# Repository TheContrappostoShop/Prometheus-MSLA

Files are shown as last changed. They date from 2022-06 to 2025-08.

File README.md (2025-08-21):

<div align="center">
  <h1>Prometheus-MSLA (LEGACY)</h1>
</div>

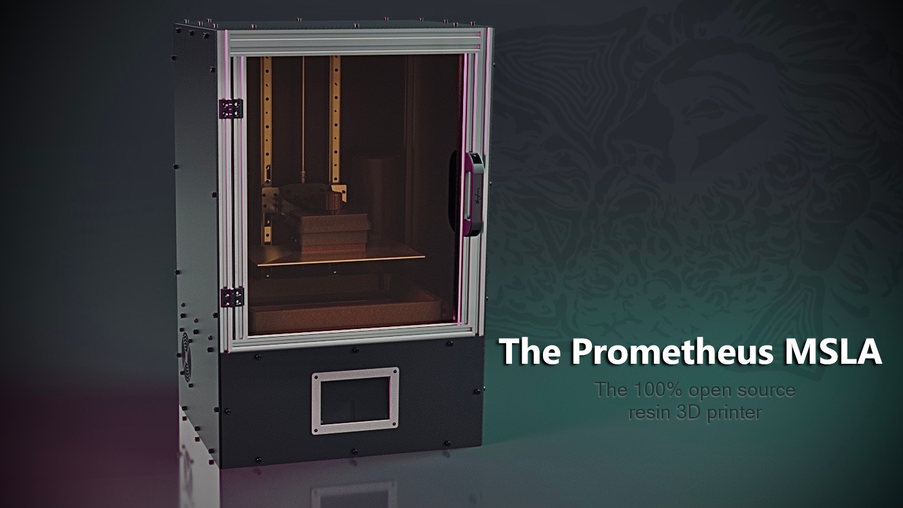
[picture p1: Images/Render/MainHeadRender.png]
Prometheus MSLA Printer Render! Open Source MSLA Printer Prometheus MSLA

Discord Link (https://discord.gg/6pFDJ3GbKh)

*DISCLAIMER ! THIS VERSION OF THE PROMETHEUS IS NOW NOT SUPPORTED DUE TO UNRELIABLE KEY COMPONENTS OF THE MACHINE SUCH AS THE LCD DUE TO DEFFECTIVE BATCHES FROM CHINESE MANUFACTURER. INSTEAD OF PATCHING THESE ISSUES, A NEW GENERATION OF PRINTER WILL BE CREATED.

The First fully open source MSLA 3D printer. The Prometheus MSLA is a large format printer with build volume of 298mm x 164mm x 350mm with a 13.7inch 7K monochrome display ( one of the largest and high resolution on the market ).

In greek mythology there is a legend of a Titan named Prometheus, he is known
for defying the gods by stealing fire and gifting it back to humanity.

Not only did he give them fire, Prometheus also taught humans how to use fire,
thus giving them the skill of metalwork, then ensued science and the arts,
allowing us to create everything we have today.

We created this project because we wanted to offer a machine that was accessible
to everyone, we wanted it to be easily modified so that you can create and give
your machine your own personal touch.

## Source and Documentation

### CAD
The full Prometheus Assembly can be viewed or downloaded over on
[GrabCAD](https://grabcad.com/library/the-prometheus-msla-v1-full-assembly-1)!

See [here](STL) for exported STLs of all of the printed parts, and
[here](Drawings) for the exported DXF files for the enclosure and base plates.

### Control Board
Prometheus Apollo Board EDA & Production Files Coming Soon!

### Firmware
For a fully configured Raspberry Pi image, check out
[PrometheusOS](https://github.com/TheContrappostoShop/PrometheusOS)!

You can also find our configuration files
[here](https://github.com/TheContrappostoShop/Prometheus_Config) for a manual
software install.

### Documentation
Finalized Build Guide Coming Soon!

In the mean-time, check out our
[Youtube Assembly Guide](https://www.youtube.com/watch?v=eP9PegG7pnA&list=PL1cx7A6ZVoZlWrnPsP4_g7WrTk8wNiGpT),
or join our Discord for advice and assistance!

## Community
If you want to share your experience or need more information, we are happy to
welcome you to our [Discord Server](https://discord.gg/GFUn9gwRsj).

## Licensing

License Statement CC BY-NC 4.0 (https://creativecommons.org/licenses/by-nc/4.0/)

This work is licensed under a <a rel="license" href="http://creativecommons.org/licenses/by-nc/4.0/">Creative Commons Attribution-NonCommercial 4.0 International License</a>.

## The Prometheus MSLA Team
|||
|-----|---|
| The Contrapposto Shop | Samuel (sam.boutin) and Melissa |
| CAD Modelling | Gil (rattus) and Shyam (eThing) |
| Electronics and Software | Paul (Paul_GD) and Ada (ragwafire) |
| The Rest of the Prometheus MSLA Team | Kristine (Elantris), Tyler, Stefan (Stuff!), Zakary, Zachary, Alain (Thewood3D) |

And thanks to all of those who helped, in one way or an other, on this open
source project!!

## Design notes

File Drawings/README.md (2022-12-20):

# Prometheus MSLA Panel & Plate Drawings
Here you can find all of the .dxf files for the enclosure panels and base/mid
plates for the Prometheus MSLA Printer.

## Enclosure Panels
All of the enclosure panels can be cut from 4mm (5/32") acrylic or ABS sheet.
The door panel should be transparent, if you wish to see inside the machine, but
beyond that basically any material may be used. Keep in mind, thicker or thinner
panels may require differently sized screws.

## Middle Plate and Base Plate
The "Middle Plate" and the "Base Plate" need to be about 12.5mm (1/2") thick.

You can use something like HDPE for easier cleaning, or even just MDF (which you
will need to seal) for a cheaper build.

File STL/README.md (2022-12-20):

# Prometheus MSLA Printed Parts STLs
Here you can find the .stl files for all of the 3D-printed parts for the
Prometheus MSLA Printer.

## Material
We recommend printing the vat in PLA or PETG! Other materials may react with the
chemicals in the resin.

The Structural parts (such as the arm) need to be very 
rigid--they can be printed in PLA, carbon fiber filled material, or other stiff
plastics.

## Print Settings
All the parts should be printed at 0.2mm layer height, with at least 35% infill
and at least 6 walls (with a .4 nozzle).

## Updates
For the latest versions of each part, see the full assembly [here](../CAD/).

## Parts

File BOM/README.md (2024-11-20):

# Bill Of Materials
> Note: Some listings on this page are affiliate links, to help support the project

| Category  | Description | Quantity  | Link  |
|---|---|---|---|
| *_Fasteners_* | | | |
| | M3 T-Nut | 18  | [Aliexpress](https://s.click.aliexpress.com/e/_DBXx7kr), [Amazon](https://amzn.to/3jPTPxT) |
| | M5 T-Nut | 137 | [Aliexpress](https://s.click.aliexpress.com/e/_DBXx7kr), [Amazon](https://amzn.to/3voWRi8) |
| | M3 Insert (L6mm)  | 46  | [Aliexpress](https://s.click.aliexpress.com/e/_DcgRRhD), [Amazon](https://amzn.to/381tYR5), [McMaster-Carr](https://www.mcmaster.com/94459A140/) |
| | M4 Insert (L6mm)  | 5 | [Aliexpress](https://s.click.aliexpress.com/e/_DcgRRhD), [Amazon](https://amzn.to/3vuExnA), [McMaster-Carr](https://www.mcmaster.com/94459A150/) |
| | M3x8 SHC | 38  | [Aliexpress](https://s.click.aliexpress.com/e/_DlgyRsJ), [McMaster-Carr](https://www.mcmaster.com/91290A113/) |
| | M3x10 SHC | 18 | [Aliexpress](https://s.click.aliexpress.com/e/_DlgyRsJ), [McMaster-Carr](https://www.mcmaster.com/91290A115/) |
| | M3x18 SHC | 8  | [Aliexpress](https://s.click.aliexpress.com/e/_DlgyRsJ), [McMaster-Carr](https://www.mcmaster.com/91290A121/) |
| | M3x20 Countersunk  | 4  | [Aliexpress](https://s.click.aliexpress.com/e/_Deg3Y3h)  |
| | M3x25 SHC | 14  | [Aliexpress](https://s.click.aliexpress.com/e/_DlgyRsJ) |
| | M3x10 Countersunk | 44  | [Aliexpress](https://s.click.aliexpress.com/e/_Deg3Y3h),[McMaster-Carr](https://www.mcmaster.com/91294A130/) |
| | M4x10 SHC | 13  | [Aliexpress](https://s.click.aliexpress.com/e/_DlgyRsJ),[McMaster-Carr](https://www.mcmaster.com/91290A144/) |
| | M5x8 SHC | 135 | [Aliexpress](https://s.click.aliexpress.com/e/_DlgyRsJ), [McMaster-Carr](https://www.mcmaster.com/91290A222/) |
| | M5x16 SHC | 22  | [Aliexpress](https://s.click.aliexpress.com/e/_DlgyRsJ), [McMaster-Carr](https://www.mcmaster.com/91290A232/) |
| | M8x50 rod (or set screw)| 1 | [Aliexpress](https://s.click.aliexpress.com/e/_Dd8sriF), [McMaster-Carr](https://www.mcmaster.com/92015A151/) |
| | M3 Nut | 6 | [Aliexpress](https://s.click.aliexpress.com/e/_DdFF1gf), [Amazon](https://amzn.to/3PisOlx), [McMaster-Carr](https://www.mcmaster.com/90592A085/) |
| | M4 Nut | 12  | [Aliexpress](https://s.click.aliexpress.com/e/_DdFF1gf), [Amazon](https://amzn.to/3FApYUP), [McMaster-Carr](https://www.mcmaster.com/90592A090/) |
| | M3 Washer | 8  | [Aliexpress](https://s.click.aliexpress.com/e/_DDZk2np), [Amazon](https://amzn.to/3FePfU3), [McMaster-Carr](https://www.mcmaster.com/93475A210/) |
| | M4 Washer | 4 | [Aliexpress](https://s.click.aliexpress.com/e/_DDZk2np), [Amazon](https://amzn.to/3HwZ4iS), [McMaster-Carr](https://www.mcmaster.com/93475A230/) |
| | M5 Washer | 13  | [Aliexpress](https://s.click.aliexpress.com/e/_DDZk2np), [Amazon](https://amzn.to/3h75RW4), [McMaster-Carr](https://www.mcmaster.com/93475A240/) |
| \*Ball Screw build | M4x16 SHC | 4 | [Aliexpress](https://s.click.aliexpress.com/e/_DlgyRsJ), [McMaster-Carr](https://www.mcmaster.com/91290A154/) |
| \*Ball Screw build | M5x35 SHC | 4 | [Aliexpress](https://s.click.aliexpress.com/e/_DlgyRsJ), [McMaster-Carr](https://www.mcmaster.com/91290A256/) |
| \*Blind Joint | M5 OR M6x12 BHC | 32  |  [Aliexpress](https://s.click.aliexpress.com/e/_DkBwHbz)  |
|||||
| *_Motion_* |
| | Nema 17 *0.9deg* (Bigger is better)| 1 | [Aliexpress](https://s.click.aliexpress.com/e/_Dl8Sp3z), [Amazon](https://amzn.to/3JTS9Ok) | [Spool3D](https://spool3d.ca/nema17-0-9-degree-stepper-motor-60mm/)
| | Linear Rails MGN12H 450mm | 2 | [Aliexpress](https://s.click.aliexpress.com/e/_DEJSeVN), [Amazon](https://amzn.to/3PisOlx),[Amazon](https://amzn.to/3uSQrbX)|
| | Coupling 5mm to 8mm | 1 | [Amazon](https://amzn.to/3xAs1Wk)|
| | Bearing | 1 | [Amazon](https://amzn.to/37tBqo3)|
| \*ACME build | ACME T8 2mm lead 500mm | 1 | [Aliexpress](https://s.click.aliexpress.com/e/_DDD1Mdz), [Amazon](https://amzn.to/3NEDFog) |
| \*ACME build | ACME Nut 2mm lead | 1 | [Spool3D](https://spool3d.ca/t8-lead-screw-anti-backlash-nut/) |
| \*Ball Screw Build 500 *ask Ali seller for coupler | Ball Screw 500mm 1204 | 1 | [Aliexpress](https://s.click.aliexpress.com/e/_DCBP8oT), [Amazon](https://amzn.to/41ezOoz)|
||||
| *_Electronics_* |
|*READ NOTES!* | LCD 7K 13.6inch | 1 | [Aliexpress](https://s.click.aliexpress.com/e/_Dex3wQn)|
|*READ NOTES!* | LCD HDMI Driver | 1 | [Aliexpress](https://s.click.aliexpress.com/e/_DeM0m83)|
|*READ NOTES!* | LCD + HDMI Driver *ALTERNATIVE* (Ask seller for driver) | 1 | [Alibaba](https://www.alibaba.com/product-detail/13-6-inch-7K-6480-3600_1600919542980.html)|
| | Inductive Probe 5v M12 NPN| 1 | [Aliexpress](https://s.click.aliexpress.com/e/_DcAIFCR), [Amazon](https://amzn.to/380BJGW)|
| | Power Supply 24v | 1 | [Aliexpress](https://s.click.aliexpress.com/e/_DdjQPYR), [Amazon](https://amzn.to/3EsALiw)|
| | IEC Socket | 1 | [Aliexpress](https://s.click.aliexpress.com/e/_DdLPQwn), [Amazon](https://amzn.to/3JSTPb1)|
| | 92mm 12v Fan | 2 | [Amazon](https://amzn.to/3rDMfL1)|
| | DSI Touch Screen | 1 | [Aliexpress](), [Amazon](https://amzn.to/3M15Rjr)|
| | DSI Flex Cable | 1 | [Amazon](https://amzn.to/3xArXWf)|
| | Raspberry pi 4B | 1 | [RPi Locator](https://rpilocator.com/?cat=PI4)|
| | Prometheus Control Board  | 1 | [Contrapposto Shop](https://www.contrapposto.shop)|
| | LED Array | 1 | [Aliexpress](https://s.click.aliexpress.com/e/_DmQAAPt)|
| | LED COB Fresnel (Alternative) | 1 | [Aliexpress](https://www.aliexpress.com/w/wholesale-sumaopai.html?spm=a2g0o.productlist.search.0)|
|||||
| *_Frame_* |
| | COMPLETE FRAME KIT (Blind joint)| 1  | [DLLPDF](https://www.dllpdf.com/prometheus-msla-structural-kit) |
| | 2020 Aluminum Extrusion - 490mm | 2  | [Aliexpress](https://s.click.aliexpress.com/e/_DCueqH9), [Amazon](https://amzn.to/3xlxGzp) |
| | 2020 Aluminum Extrusion - 450mm | 2  | [Aliexpress](https://s.click.aliexpress.com/e/_DCueqH9), [Amazon](https://amzn.to/3xhM6Ax) |
| | 2020 Aluminum Extrusion - 412mm | 6  | [Aliexpress](https://s.click.aliexpress.com/e/_DCueqH9), [Amazon](https://amzn.to/3xhM6Ax) |
| | 2020 Aluminum Extrusion - 410mm | 2  | [Aliexpress](https://s.click.aliexpress.com/e/_DCueqH9), [Amazon](https://amzn.to/3KoJ3KC) |
| | 2020 Aluminum Extrusion - 324mm | 6  | [Aliexpress](https://s.click.aliexpress.com/e/_DCueqH9), [Amazon](https://amzn.to/3LNUVpG) |
| | 2020 Aluminum Extrusion - 705mm | 4  | [Aliexpress](https://s.click.aliexpress.com/e/_DCueqH9), [Amazon](https://amzn.to/3jmZhIf) |
| | Hinges | 2  | [Amazon](https://amzn.to/3jthnZ2) |
| \*Can replace by blind joint | Hidden connector | 36 | [Amazon](https://amzn.to/3Mbfa15) |
| \*Can be hand made or locally source  | Base plate | 1  | [DLLPDF](https://www.dllpdf.com/prometheus-msla-base-plate) |
| \*Can be hand made or locally sourced | Middle LCD plate | 1  | [DLLPDF](https://www.dllpdf.com/prometheus-msla-mid-base) |
|||||
| *_Misc_* |
| | Neodimium Magnet 12x3mm | 2 | [Aliexpress](https://s.click.aliexpress.com/e/_DBFfQbD), [Amazon](https://amzn.to/3WKNjeT)|
| \*Can be approximative | Spring 10.5mm Lg / 7.1mm OD | 6 ||
| | BallDetent M8x12 | 2 | [Aliexpress](https://s.click.aliexpress.com/e/_Ddmoasj), [Amazon](https://amzn.to/3MggyzN)|
| | 6mm Glass 302mm x 176.6mm | 1 ||
| | Ferrule Kit | 1 | [Amazon](https://amzn.to/3GTaqvl)|
| | FEP (at least 250x350mm) | 1 | [Spool3D](https://spool3d.ca/fep-film-100-micron/) |
|||||
| *_Cables_* |
| |Micro to HDMI Cable 8k	 | 1 | [Aliexpress](https://s.click.aliexpress.com/e/_DDA2nlt), [Amazon](https://amzn.to/3wXmHMc) |
| |Mini USB cable 	 | 1 | [Aliexpress](https://s.click.aliexpress.com/e/_DBPXo9l) |
| | 16 AWG cable		 | | |
|||||
| *_Aluminum Parts_* |
| | COMPLETE FRAME KIT | 1 | [DLLPDF] (https://www.dllpdf.com/prometheus-msla-structural-kit) |
| | Build Plate | 1 | [DLLPDF](https://www.dllpdf.com/prometheus-msla-build-plate)|
| | Arm | 1 | [DLLPDF](https://www.dllpdf.com/prometheus-msla-arm-support)|
| | Rails Link  | 1 | [DLLPDF](https://www.dllpdf.com/prometheus-msla-rails-link)|
|||||
| *_3D Printed Parts_* |
| | Arm Plate Link | 1 ||
| | Arm Spacer | 1 ||
| | Bearing Holder | 1 ||
| | Build Plate Link | 1 ||
| | Build Plate Top | 1 ||
| | Door Handle | 1 ||
| | Knob | 1 ||
| | LCD Driver Braket | 1 ||
| | LCD Insert | 1 ||
| | Motor Mount | 1 ||
| | Pour Shield | 1 ||
| | Probe Trigger | 1 ||
| | Touch Screen Braket1 | 1 ||
| | Touch Screen Braket2 | 1 ||
| | Touch Screen Frame | 1 ||
| | Vat Body | 1 ||
| | Vat Bottle Docking Station | 1 ||
| | Vat Latch Left | 1 ||
| | Vat Latch Rear | 1 ||
| | Vat Latch Right | 1 ||
| | Vat Retainer Ring | 1 ||
| | Vat Handle | 2 ||

** PROBLEM WITH LCD MANUFACTURER ! We have encounter a problem with the suggested LCD and driver part. For now, only one member of our team have this problem. We are trying to have answers from the manufacturer because it seems only the "newer" LCDs have issues. We are currently looking for an upgrade version. Buy the one listed at your own risk. More details on Discord. 

** We recommend printing the vat in PLA, PETG or PC! Other materials may react with the chemicals in the resin

** The Structural parts (such as the arm) need to be very rigid and stiff! They can be printed in PLA, carbon fiber filled material, or other stiff plastic

** All the parts are printed at 0.2mm layer height, with at least 35% infill and at least 6 walls (.4 nozzle)

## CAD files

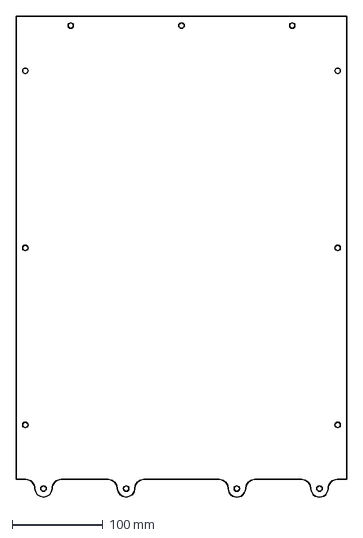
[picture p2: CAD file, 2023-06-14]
Drawings/Top_Right.dxf
364.0 x 529.9 mm

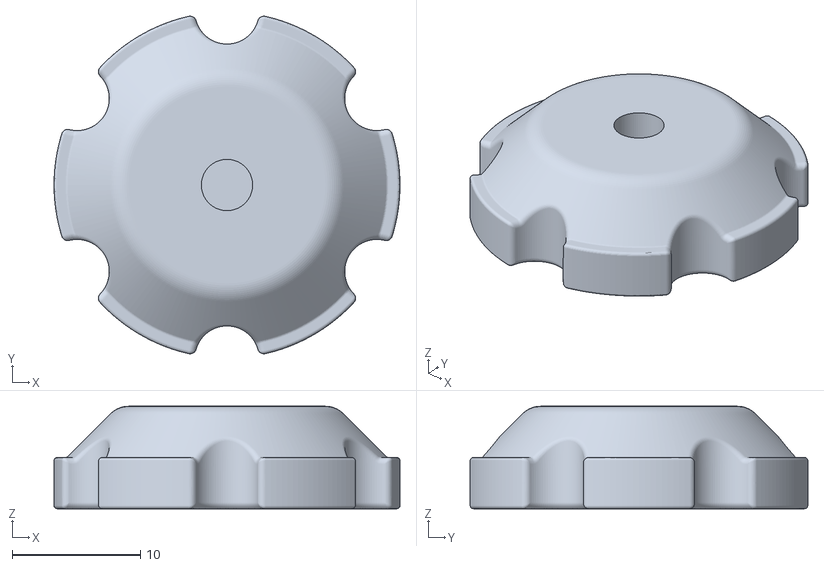
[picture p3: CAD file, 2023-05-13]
STL/Bottle Plunger.stl
27.0 x 26.4 x 8.00

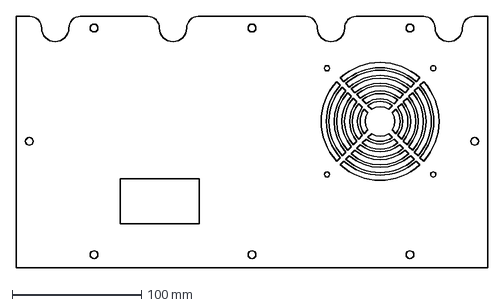
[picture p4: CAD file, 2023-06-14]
Drawings/Base_Rigth.dxf
364.0 x 194.0 mm

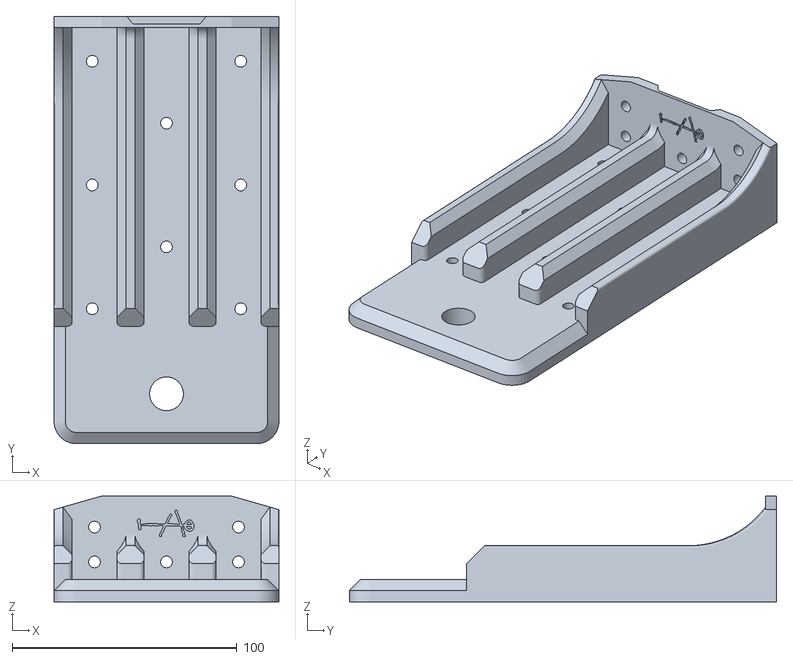
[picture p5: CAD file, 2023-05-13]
STL/Arm Plate Link.stl
100.0 x 190.0 x 47.0

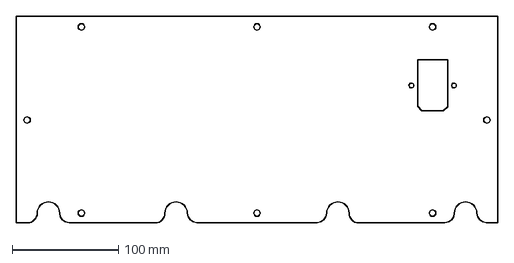
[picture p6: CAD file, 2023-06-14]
Drawings/Base_Rear.dxf
452.0 x 194.0 mm

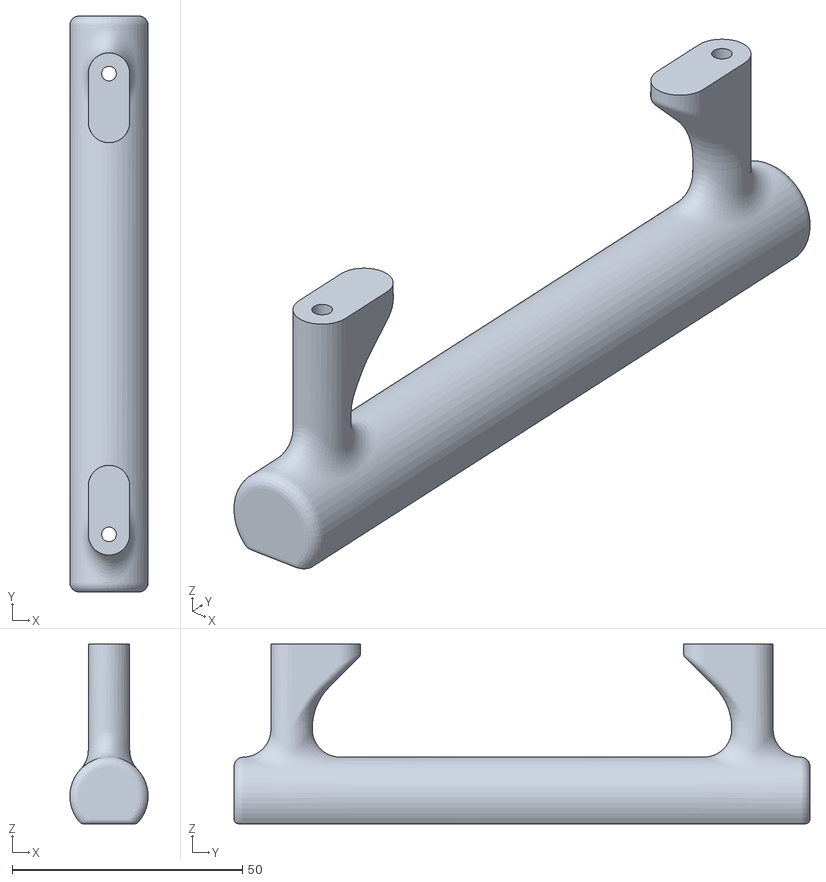
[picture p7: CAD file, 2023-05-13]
STL/Vat Handle.stl
17.0 x 125.0 x 39.0

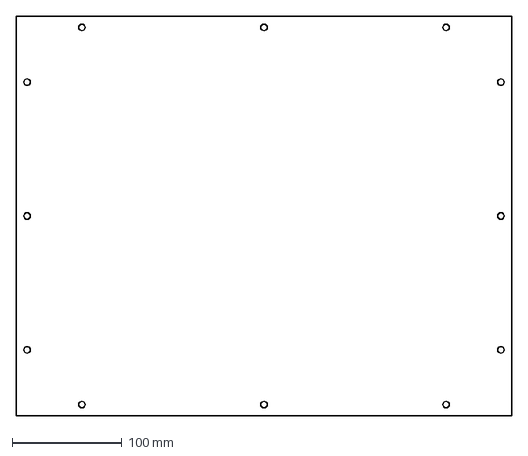
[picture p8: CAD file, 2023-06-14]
Drawings/Top.dxf
452.0 x 364.0 mm

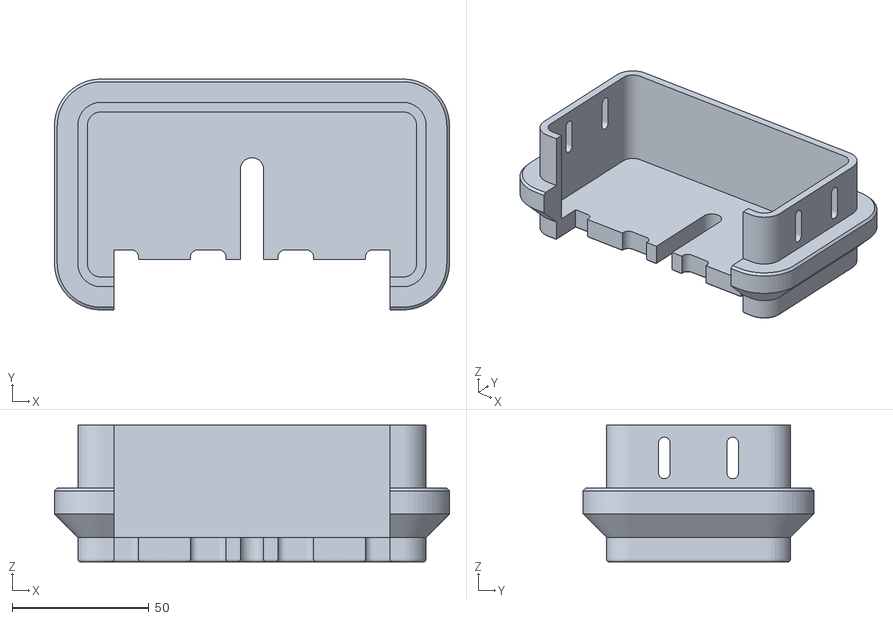
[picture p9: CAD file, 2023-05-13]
STL/Build Plate Top.stl
144.4 x 84.4 x 50.0

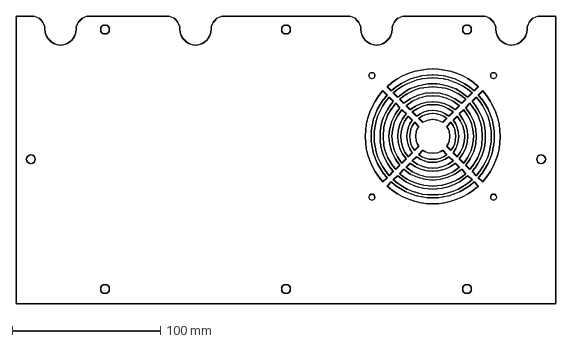
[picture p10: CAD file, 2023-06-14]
Drawings/Base_Left.dxf
364.0 x 194.0 mm

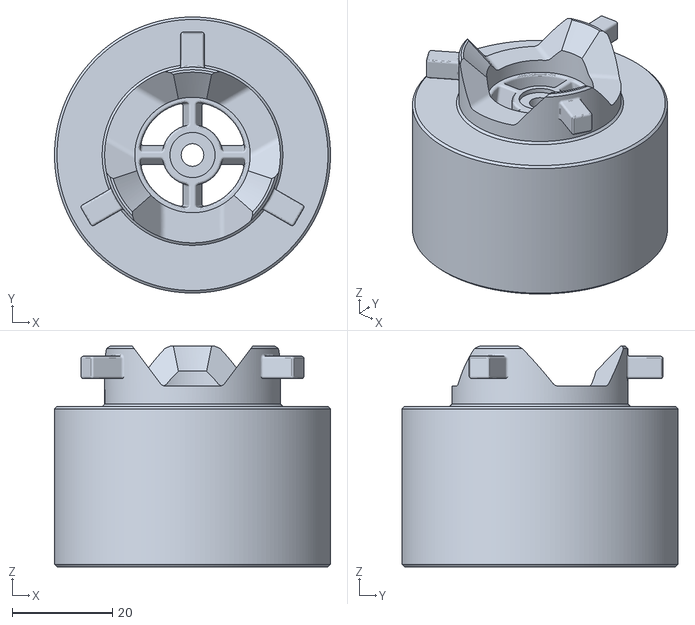
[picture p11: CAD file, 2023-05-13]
STL/Bottle Cap.stl
55.0 x 55.0 x 44.0

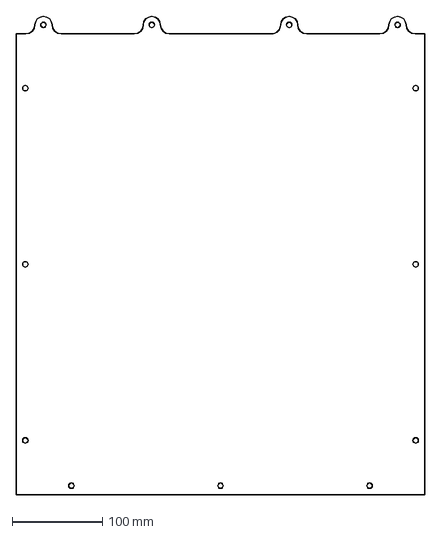
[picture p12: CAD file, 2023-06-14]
Drawings/Top_Rear.dxf
452.0 x 529.5 mm

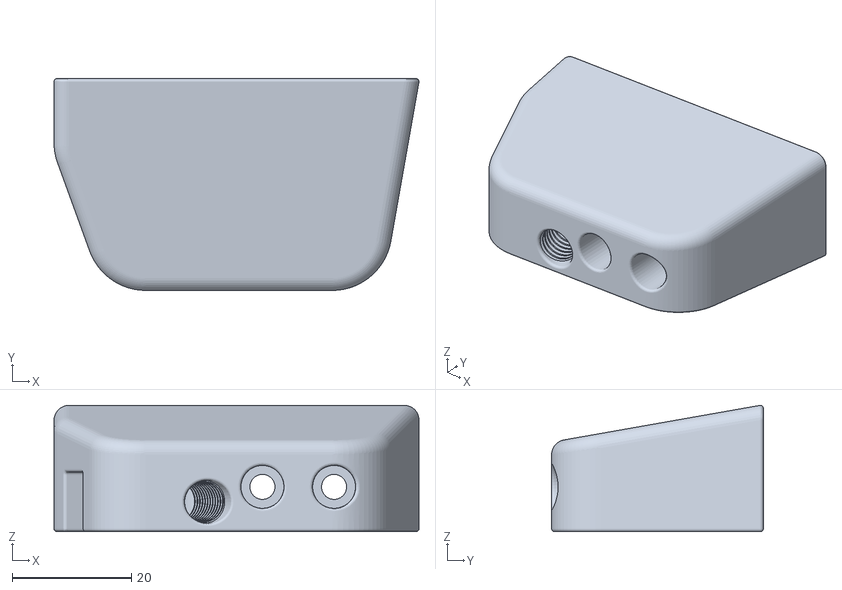
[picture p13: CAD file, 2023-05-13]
STL/Vat Latch Left.stl
61.2 x 35.5 x 21.2

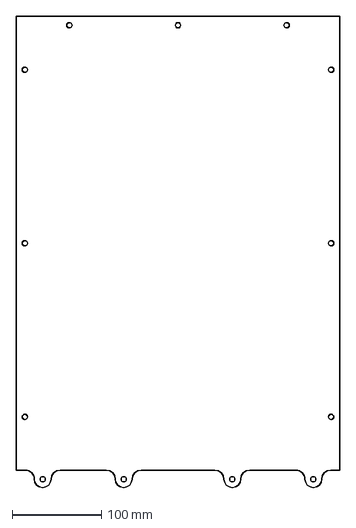
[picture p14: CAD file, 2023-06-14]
Drawings/Top_Left.dxf
364.0 x 529.5 mm

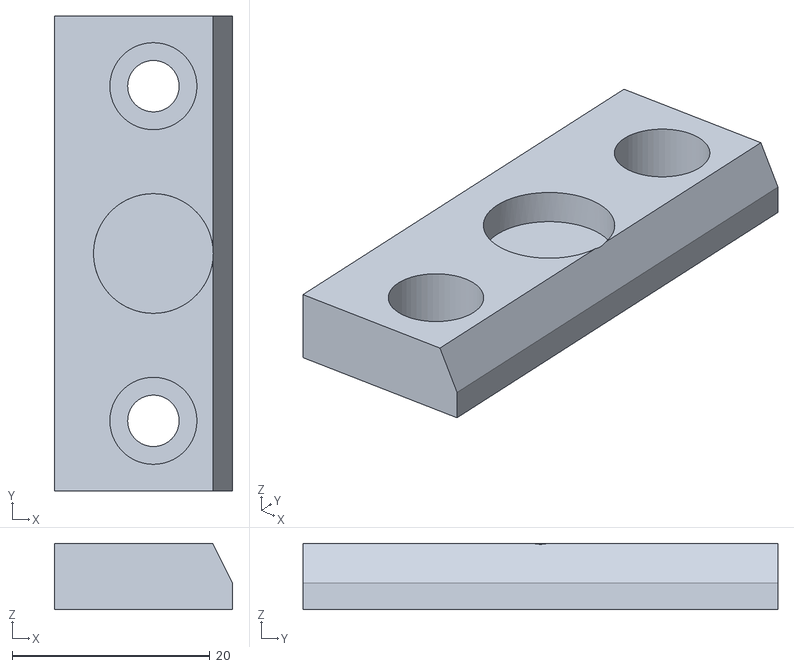
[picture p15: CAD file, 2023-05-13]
STL/Magnet Door.stl
18.0 x 48.0 x 6.70

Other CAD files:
Drawings/Door.dxf
STL/Arm Spacer.stl
Drawings/Base_Plate.dxf
STL/Touch Screen Frame.stl
Drawings/Base_Front.dxf
Drawings/Middle Plate ACME.dxf
Drawings/Middle Plate BallScrew.dxf
Drawings/MiddlePlate.dxf
STL/BK10 Holder.stl
STL/Ball Screw Spacer.stl
STL/Bearing Holder.stl
STL/Build Plate Link.stl
STL/Door Handle.stl
STL/Knob.stl
STL/LCD Driver Braket.stl
STL/LCD Insert.stl
STL/LED Driver Braket.stl
STL/LED Support.stl
STL/M5 Spacer.stl
STL/Magnet Door Stopper.stl
STL/MotherBoard Braket.stl
STL/Motor Mount.stl
STL/PSU Braket.stl
STL/Pi Pannel.stl
STL/Pi Spacer.stl
STL/Pour Shield.stl
STL/Probe Trigger.stl
STL/Touch Screen Braket1.stl
STL/Touch Screen Braket2.stl
STL/Vat (without refill).stl
STL/Vat Body.stl
STL/Vat Bottle Docking Station.stl
STL/Vat Latch Rear.stl
STL/Vat Latch Right.stl
STL/Vat Retainer Ring.stl

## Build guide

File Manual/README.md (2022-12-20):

# Prometheus MSLA Build Instructions
Written build manual coming soon!

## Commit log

2022-05-07 new STL Folder
2022-05-26 Revert "new STL Folder"
    This reverts commit db2a1d6b05b6e94fadcd6e185e5e9742db9d17d8.
2022-06-04 Upload STLs
    Upload first version of STL folder
    [Arm Plate Link.stl, Arm Spacer.stl, Bearing Holder.stl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]
2022-06-11 Import DXF
    DXF file V1 for pannels
    [BDown.dxf, BTop.dxf, BasePlate.dxf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]
2022-06-11 Update Latch STL
    Update latch stl left and right
    [Vat Latch Left.stl, Vat Latch Right.stl]
2022-06-13 new BOM folder, big picture of license and link
2022-06-19 STL correction
    adding Vat handle STL and replace vat body with new version
    [Vat Body.stl, Vat Handle.stl]
2022-06-19 Add STLs + BOM + CAD
    adding new STLs for magnet, the BOM in two formats and the CAD for the machine
    [MAGNET DOOR.stl, Magnet Door Stopper.stl, Prometheus MSLA BOM.xlsx]
2022-06-19 Remove wrong CAD
2022-06-19 Added CAD Model
    [PrometheusMSLAAssembly.step]
2022-06-19 Create Prometheus MSLA Assembly.step
    [Prometheus MSLA Assembly.step]
2022-10-27 Add Markdown table to BOM/README.md
2022-11-03 Add Links to BOM Fastener section
    Added McMaster and Amazon links for most entries
2022-11-26 Adding missing STLs
    adding missing stl for resin bottle + new vat
    [Bottle Cap.stl, Bottle Plunger.stl]
2022-11-26 Updates 2022-11-26
    Updates on some of the design. Modification and replacement of some STLs and in general CAD. Updates BOM.
    [Door.dxf, LCD Insert.stl, LED Driver Braket.stl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]
2022-11-26 Adding/Update DXF
    Update on old DXF middle plate and add the BallScrew one
    [Middle Plate ACME.dxf, Middle Plate BallScrew.dxf]
2022-12-10 Finish rewriting BOM sections in markdown (#7)
    * Finish rewriting BOM sections in markdown
    * Rewrite the notes at the bottom
    * Update Hardware amazon links
    replace the existing amazon links by affiliates one
2022-12-18 Add link for board launch (#9)
2022-12-20 Update BOM qty
2022-12-21 Update BOM links
    Update of the links for online store ( contrapposto.shop and dllpdf.com )
2023-01-29 Update README.md
    Changed Linear Rails Size from 400mm to 450mm to match the CAD model
2023-01-29 Braket Fix
    [LED Driver Braket.stl, PSU Braket.stl]
2023-02-23 Add STLs spacers
    STLs spacers to adapt to the 3mm thick base plate from DLLPDF
    [M5 Spacer.stl, Pi spacer.stl]
2023-02-23 Adding DLLPDF dxf kit
    The DLLPDF dxf is the same used for the panel kit
    [DLLPDF_base_Left.dxf, DLLPDF_base_front.dxf, DLLPDF_base_rear.dxf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]
2023-03-06 Add STLs and Updates
    The Pi pannel was missing and the Vat without auto refill was added. The Vat handles was modified.
    [Pi Pannel.stl, Vat (without refill).stl, Vat Handle.stl]
2023-03-20 Delete old ball screw holder
    replaced by BK12/BF12
    [Ball Screw Holder.stl]
2023-03-20 Replace/Add ball screw holder
    Adding BK10, BF10 and replace BK12, BF12
    [BF10 Holder.stl, BK10 Holder.stl]
2023-03-22 Update readme
    adding specs of the printer
2023-03-25 BF10 BK10 fixed
    fixing the nuts holes
    [BF10 Holder.stl, BK10 Holder.stl]
2023-03-28 Update part
    replacing and updating the arm plate link for the ball screw compatibility
    [Arm Plate Link.stl]
2023-04-03 Update BOM
    adding 500mm ballscrew
2023-05-13 Update STL + printing orientation
    Update few parts and right orientation for printing
    [Arm Plate Link.stl, Arm Spacer.stl, Ball Screw Spacer.stl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]
2023-06-14 Update BOM README.md
2023-06-14 Update DXF + name
    Update the DXF due to misalignment for the door panel
    [Base_Front.dxf, Base_Left.dxf, Base_Plate.dxf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]
2023-06-27 Update BOM
    Update the BOM fasteners quantity
2023-10-06 Update README.md
    update spring quantity
2023-10-12 Update README.md
    update insert description
2024-08-14 Update README.md
    update magnets links
